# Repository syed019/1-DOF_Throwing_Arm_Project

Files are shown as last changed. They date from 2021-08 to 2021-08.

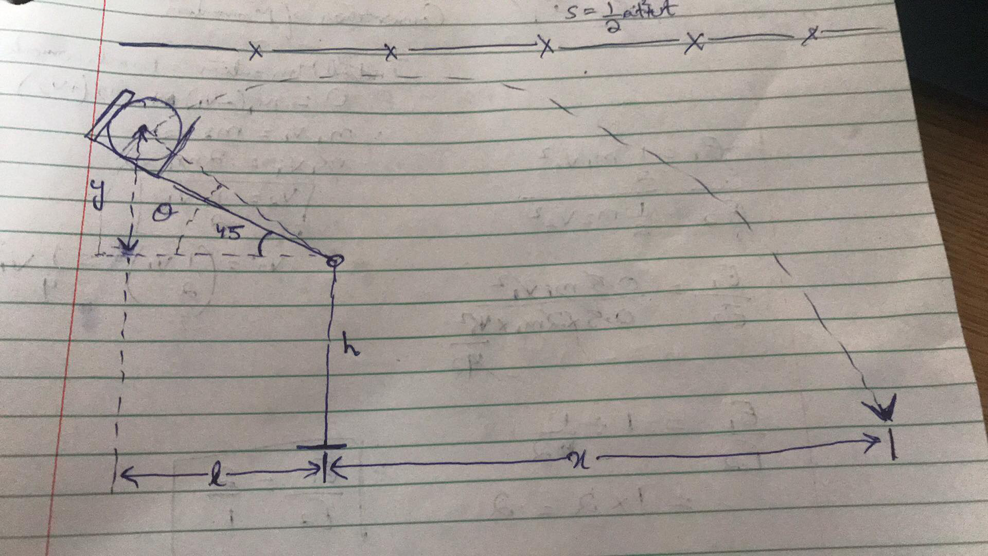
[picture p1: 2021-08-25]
Integration/1.jpg

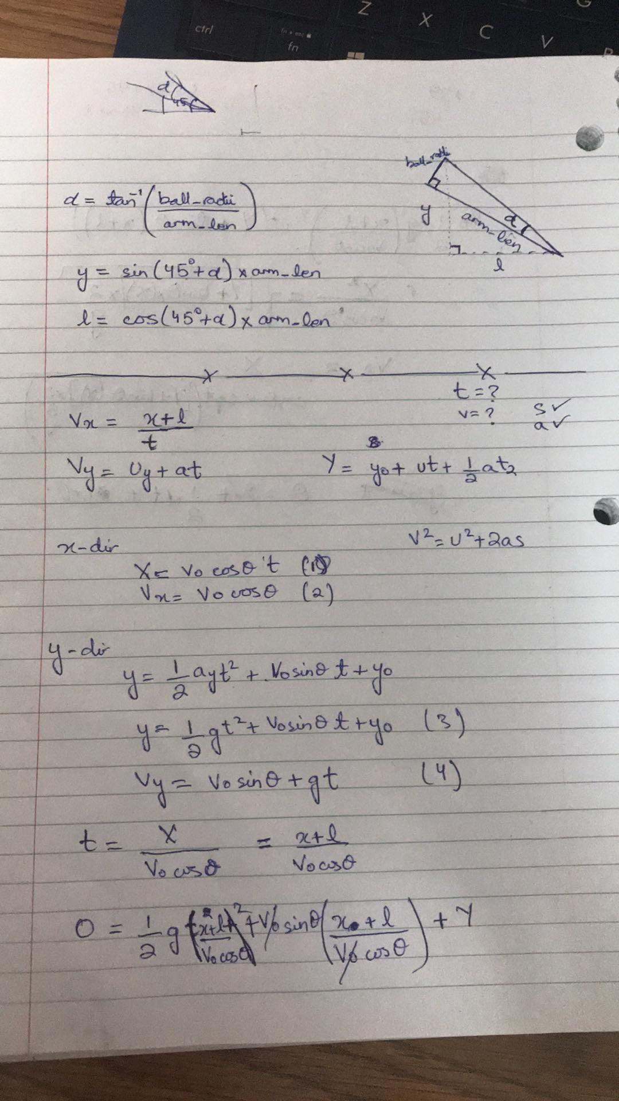
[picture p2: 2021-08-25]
Integration/2.jpg

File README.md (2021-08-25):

# MSE-312_Throwing-Arm-Project

   

This repository is for a course project (Mechatronics Design-II), taken at SIMON FRASER UNIVERSITY.

      The project consists of;
          1. Mechanical Design for a Throwing Arm (It's SOLIDWORKS design and MATLAB SIMSCAPE model)
          2. Electrical/Electronics DC-Moter Model, and it's Control Algorithm
          3. Overall Intergration of the Project

      Following are the team members for this project;
            1. Abdullah Tariq
            2. Junaid Jawed Khan
            3. Syed Imad Azeem Rizvi

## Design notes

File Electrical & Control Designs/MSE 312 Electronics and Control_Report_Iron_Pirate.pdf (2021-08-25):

# MSE312

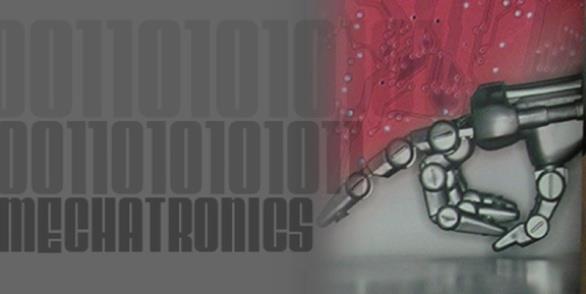
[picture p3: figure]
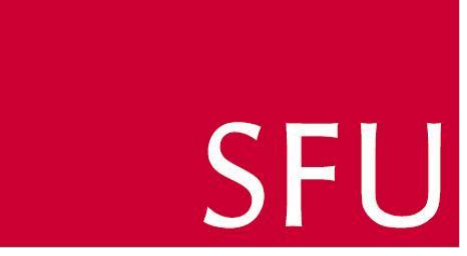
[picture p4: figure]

### ELECTRONIC & CONTROL DESIGN REPORT

Student Name | Student ID
Abdullah Tariq | 301297687
Junaid Jawed Khan | 301308300
Syed Imad Azeem Rizvi | 301297227

## Report due date: 25

th

## , JULY 2021

## Prepared for: Dr. Mehrdad Moallem

MSE-312 / MECHATRONIC DESIGN - II

MECHATRONIC SYSTEMS ENGINEERING

SCHOOL OF APPLIED SCIENCE

SIMON FRASER UNIVERSITY

i

## Table of Contents

ii

iii

## List of Figures

iv

Figure 31: Closed-Loop Speed Response | 34
Figure 32: Closed-Loop Position Response | 35

## List of Tables

Table 1: H-Bridge Cases Evaluation | 3
Table 2: Motor Comparison for RPM and Continuous Torque | 8
Table 3: Important results of each shortlisted motor | 10
Table 4: Simulink DC motor model parameters | 12
Table 5: GM8724S009 important parameters | 17
Table 6: Current, Speed and Position controller desired characteristics | 19
Table 7: Current Loop controller gains | 33
Table 8: Speed Loop controller gains | 34
Table 9: Position Loop controller gains | 35
Table 10: Open Loop Analysis | 36
Table 11: Closed Loop Analysis | 37

## 1. Introduction

The primary goal of this project was to develop a system for throwing a ball a predetermined

distance. We presented three different mechanical designs in the previous report, and after

analyzing their structures, we decided that the throwing ball bot would be our main design.

We will discuss three major aspects of the project in this report: electronic design, control design,

and their integration with our chosen mechanical design. As we are building a power circuitry for

driving a DC motor carrying an inertial load, the first section of the report will provide a detailed

analysis of its electronics. MOSFETs, H-bridges, and other necessary components are included in

the design, as well as an evaluation of their performance under various thermal conditions.

As we will be using a feedback controller to control the motor speed and position, the second part

of the project will involve implementing the control algorithm on our system. In this section, we

will first analyze our electronic system by determining its stability as well as the position of its

poles and zeros. Then, in accordance with that, we will construct a feedback loop comprised of

either P, PI, or a PID controller. Once the model for speed and position of motor control is created,

we will simulate our system and note different parameter values with different plots to obtain an

adequate value for the selected controller gains.

## 2. Electronic Design

This section of the report discusses the project's electronic design. To achieve the required

projectile motion for the ball, a DC motor is required to drive the throwing arm at a desired angular

velocity. The primary goal of this section is to design and simulate a power electronic drive

circuitry for a DC motor, which drives the arm used to throw the ball. We have included the

following components for the operation of the DC motor: An H-Bridge Circuit, a current sensor,

a PWM controlled voltage source, and a DC voltage source.

### 2.1. Power Circuitry Design

2.1.1. H-Bridge Circuit (TB6568KQ)

An H-bridge circuit is used to change the direction of a motor; in other words, it is an electronic

circuit that changes the polarity of a voltage-applied across the motor.

Figure 1 depicts a transistor-based H-bridge circuit. As seen in the diagram, two types of transistors

are used: PNP and NPN. We know from transistor electronics that when current is applied at its

base, the transistor will conduct. We can also note that the PN junction diodes are used as

freewheeling diodes, releasing electrical energy even when the motor is turned off.

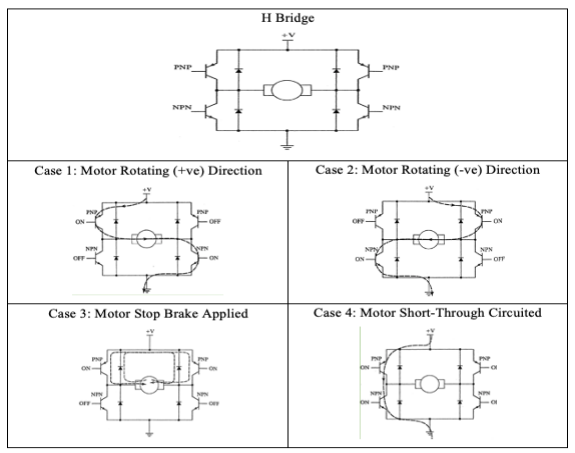
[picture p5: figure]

Figure 1: H-Bridge Operation Scenarios

Table 1: H-Bridge Cases Evaluation

SW1 | SW2 | SW3 | SW4 | MODE
OPEN | OPEN | OPEN | OPEN | OFF
CLOSED | OPEN | OPEN | CLOSED | CW
OPEN | CLOSED | CLOSED | OPEN | CCW
CLOSED | CLOSED | CLOSED | CLOSED | INVALID

With reference to Figure 1 and Table 1, if PNP (left) and NPN (right) are both turned on, the motor

will rotate clockwise. If both PNP (right) and NPN (left) are turned on, the motor will rotate

counterclockwise. If both left transistors are turned on and both right transistors are turned off, a

short circuit is formed. Dynamic or regenerative braking can be performed by turning on both

upper transistors while turning off both lower transistors. The duty cycle can be changed to control

the motor's speed.

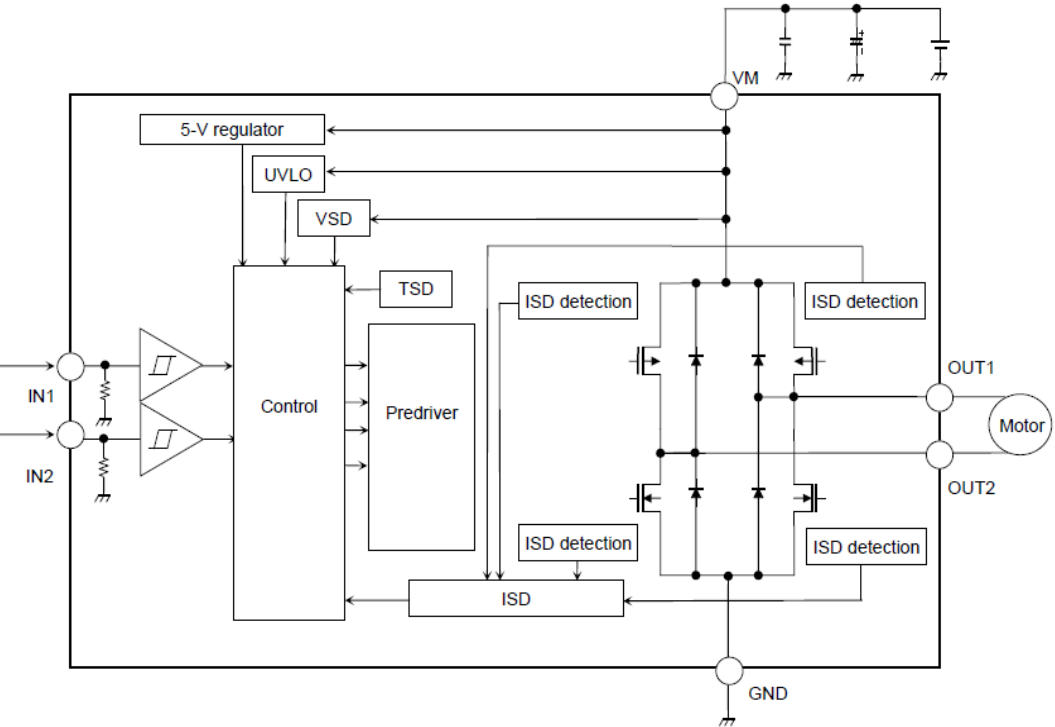
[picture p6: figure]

Figure 2: H-Bridge TB6568KQ

The motor driver we used for our motor control is the TB6568KQ. The functional block diagram

of the driver is shown in Figure 2. The TB6568KQ is a full bridge DC motor driver IC that uses

the MOS process for output power transistors. Aside from providing bidirectional motor control,

the IC includes several protection circuits that protect the motor from overcurrent, overvoltage,

thermal effects, undervoltage, and shoot through current.

Figure 3 is the data sheet of TB6568KQ H-bridge driver. This datasheet will be referenced in the

Heat Sink design section of this report.

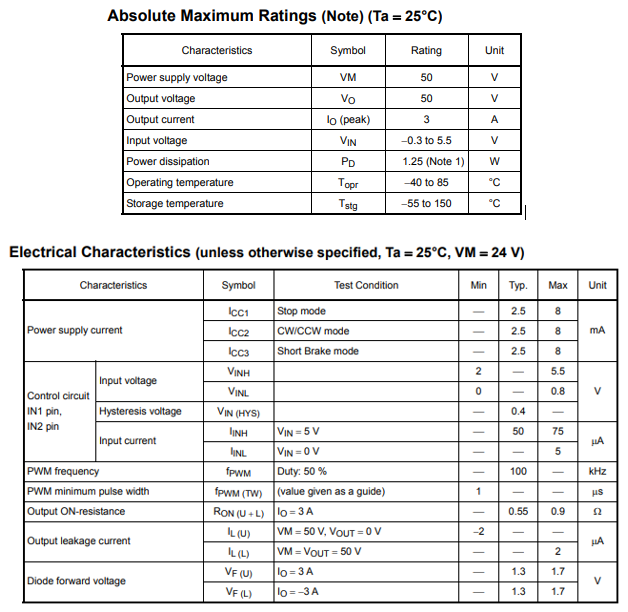
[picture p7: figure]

Figure 3: H-Bridge (TB6568KQ) Datasheet

2.1.2. Current Sensor

In our design, we will use a current sensor, which is an electronic device that detects current and

then generates a signal proportional to that value.

The basic principle for current sensing devices is that current flowing through a conducting wire

generates a magnetic field around it and uses two approaches: direct and indirect.

Direct sensing is based on Ohm's law, whereas indirect sensing is based on Faraday's and Ampere's

laws. As shown in Figure 4, we will use a built-in MATLAB Simulink block for current sensing

in our simulation.

Figure 4: Current Sensor Block

The use of a current sensor will be critical in the control portion of our project because we will

need to measure the armature current to implement feedback control of the motor current.

2.1.3. Heat Sink Design

Heat sinks are one of the most effective components for thermal management in electronics. Its

primary function is to direct heat away from the hot device. While operating, electronic

components can generate a significant amount of heat, and overheating can lead to component

failure. As a result, designing a heat manager for them is critical. The magnitude of heat generation

is directly related to power dissipation or the surface area of the electronic case from which power

is dissipated, the greater the power dissipation or the smaller the surface area, the greater the

generated heat. In other words, by increasing the surface area of our electronic case, we can reduce

the risk of overheating.

In our project, the major source of heat generation is the H-bridge driver (TB6568KQ). Figure 5

shows the thermal characteristics of this driver.

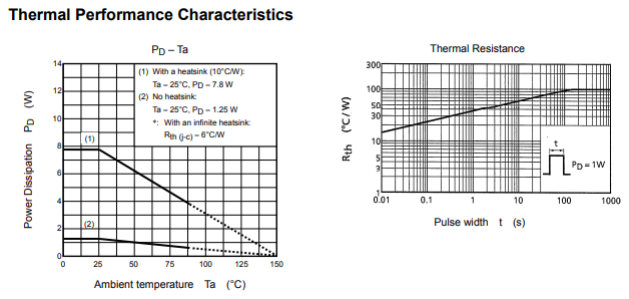
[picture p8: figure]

Figure 5: Thermal characteristics of H-Bridge.

The key point from the above figure is that if we operate our motor in the region covered by graph

2, we don't need a heatsink. However, if we want to run the motor anywhere between graphs 1 and

2, we'll need a heatsink to keep the H-bridge from overheating.

The thermal calculation for this component is as follows:

Based on the data sheet of TB6568KQ shown in Figure 5, the ambient temperature and maximum

junction temperature are defined as 25˚C and 150˚C.

The maximum power dissipated by the H-bridge can be calculated as in Equation 1.

PD = I0

2
∗ RH−bridge

PD = (3) ∗ (0.9)

PD = 8.1 Watts

Equation 1

Thermal resistance between the junction is defined as shown in Equation 2.

θjc = 6°c/w | Equation 2

The thermal resistance between junction and ambient can be calculated as shown in Equation 3.

θjc =

Tjunction,max − Tamb
PD

θjc =

150° − 25°
8.1

Equation 3

θjc = 15.43 c/w

The thermal resistance between the case and the ambient can be calculated as shown in Equation

4.

θJA = θCA + θJC

θJA = θCA − θJC

θJA = 9.432°c/w

θJA = 6°c/w

Equation 4

Finally, the case area required to dissipate the generated heat can be calculated as shown in

Equation 5.

Areq = (
50

θJA

)

2
cm²
Areq = 28.101 cm² | Equation 5

### 2.2. Motor Selection

We were given the option of choosing our own motor for this project. To complete the project's

deliverables, we selected the three motors listed below based on their respective features and

specifications that met our project requirements.

- Motor 1: GM8224S009
- Motor 2: C23-L33 W10
- Motor 3: PC280LG-011

Our goal is to simulate the operations of the three motors to evaluate their performance when

subjected to a desired inertial load.

Table 2 shows the important features of the three shortlisted motors. This table was populated

using the datasheets of the respective motor.

Table 2: Motor Comparison for RPM and Continuous Torque

Motor | Rated RPM | Rated Continuous Torque (Nm)
GM8224S009 | 720 | 0.1
C23-L33 W10 | 4700 | 0.117
PC280LG-011 | 8200 | 0.0255

Appendix A contains datasheets for the three motors that were shortlisted. In the following section,

we will analyze the behavior of the short-listed motors to choose our final motor for the controller

design.

2.2.1. Motors’s comparison:

In this section, the motors shortlisted in Section 2.2 are compared with each other. The Simulink

model in Figure 9 will be simulated with a duty cycle of 75% and the DC motor parameters will

be changed according to the shortlisted motors

Figures 6, 7 and 8 are the resultant currents, speed, and torque of each motor for a duty cycle of

75%.

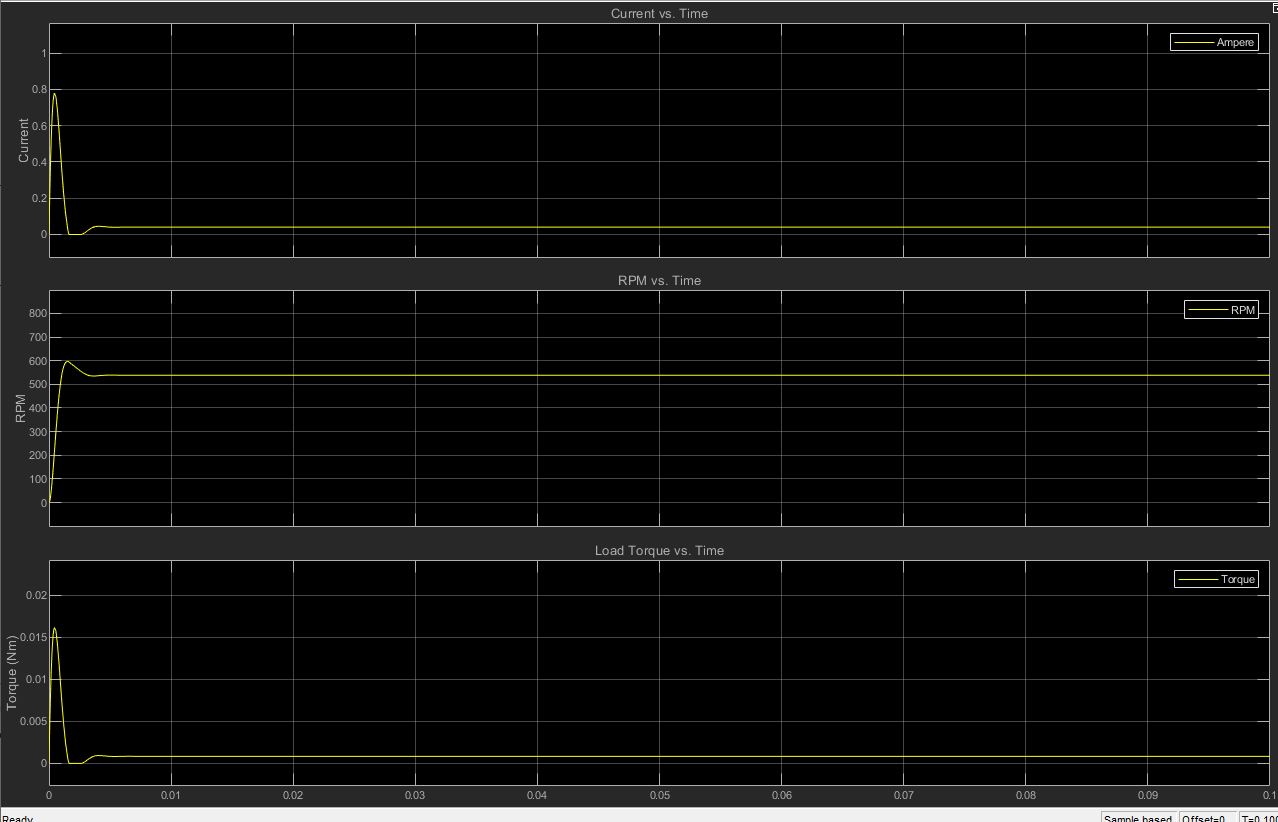
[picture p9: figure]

Figure 6: Motor 1 Resultant Current, RPM, and Torque for a 75% duty cycle.

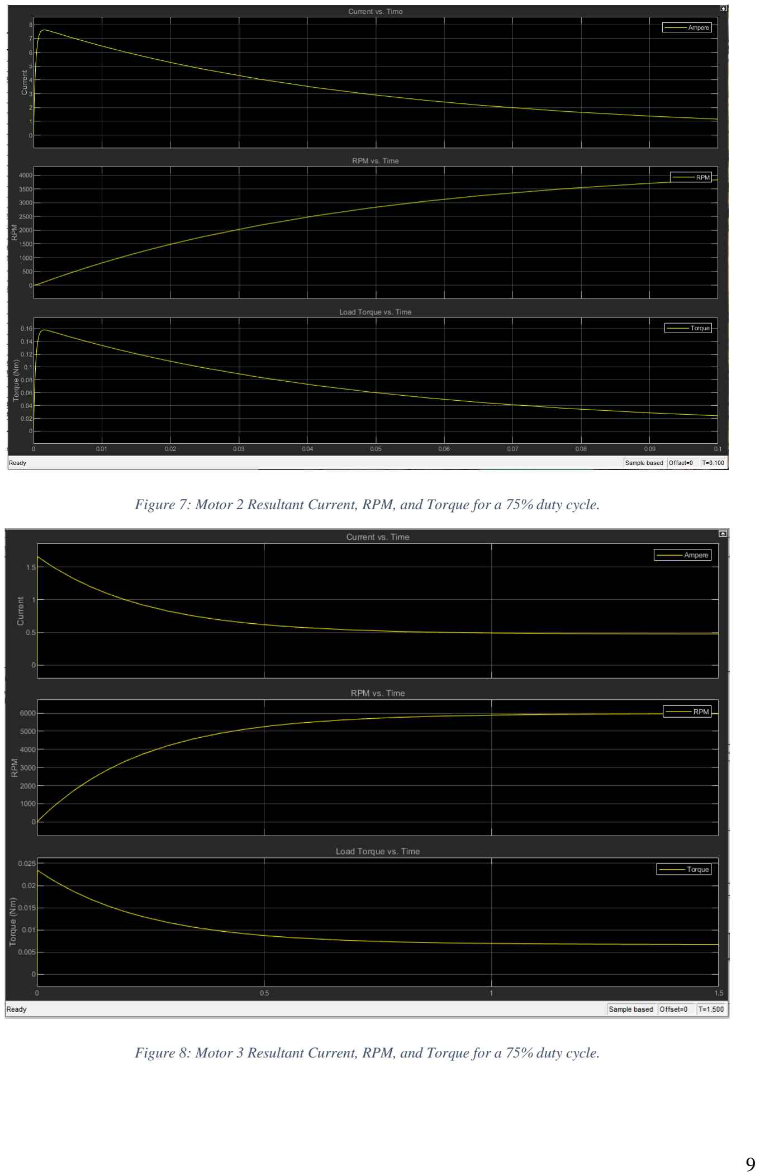
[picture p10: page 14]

Figure 7: Motor 2 Resultant Current, RPM, and Torque for a 75% duty cycle.

Figure 8: Motor 3 Resultant Current, RPM, and Torque for a 75% duty cycle.

Table 3 below illustrates the all the important parameters of each motor’s simulation results that

will be used for selecting the optimal motor for our project.

Table 3: Important results of each shortlisted motor.

Duty Cycle 75% | Motor 1 | Motor 2 | Motor 3
RPM | 539 rpm | 4370 rpm | 5970 rpm
Current | 40.62 mA | 233.575 mA | 474.797 mA
Torque | 8.41e-4 Nm | 4.461 e-3 Nm | 6.695e-3 Nm
Time to reach Steady State | 0.472 s | 0.353 s | 1.558s

The motor speed and torque data in the Table 3 were expected based on the motor data sheets in

Appendix A. Motor 3 has the highest no-load speed, whereas Motor 1 has the slowest. The system's

torque was greatest for Motor 3 to achieve its no-load speed. As higher torque is required to achieve

high speed, Motor 1 had the lowest torque due to its lower no-load speed.

Another important consideration when choosing a motor is the time it takes for the motor to reach

a steady state. According to Table 3, Motor 2 took the shortest time to reach steady state, while

Motor 3 took the longest.

Based on the preceding discussion, Motor 1 requires the least amount of electromagnetic torque to

generate enough rpm to drive the arm. As a result, we decided to use Motor 1 for our throwing

arm project. However, there is a trade-off between Motors 1 and 2 in terms of the time required to

reach no-load speed, but the time difference is not significant enough to affect our controller design

criteria.

### 2.3. Simulation of a DC Motor

In this section, we will first look at the simulation results of a DC motor using MATLAB Simulink

in three different scenarios:

1) PWM and Average Mode Simulation
2) With and Without Gear Reduction Simulation
3) With and Without Gear Reduction Simulation

The output behavior of motor parameters will be discussed and compared in each case, followed

by a comparison of the three shortlisted motors by varying the duty cycle of their PWM signal.

Figure 9 shows the designed Simulink model of a DC motor employed for analysis in this section

of the report.

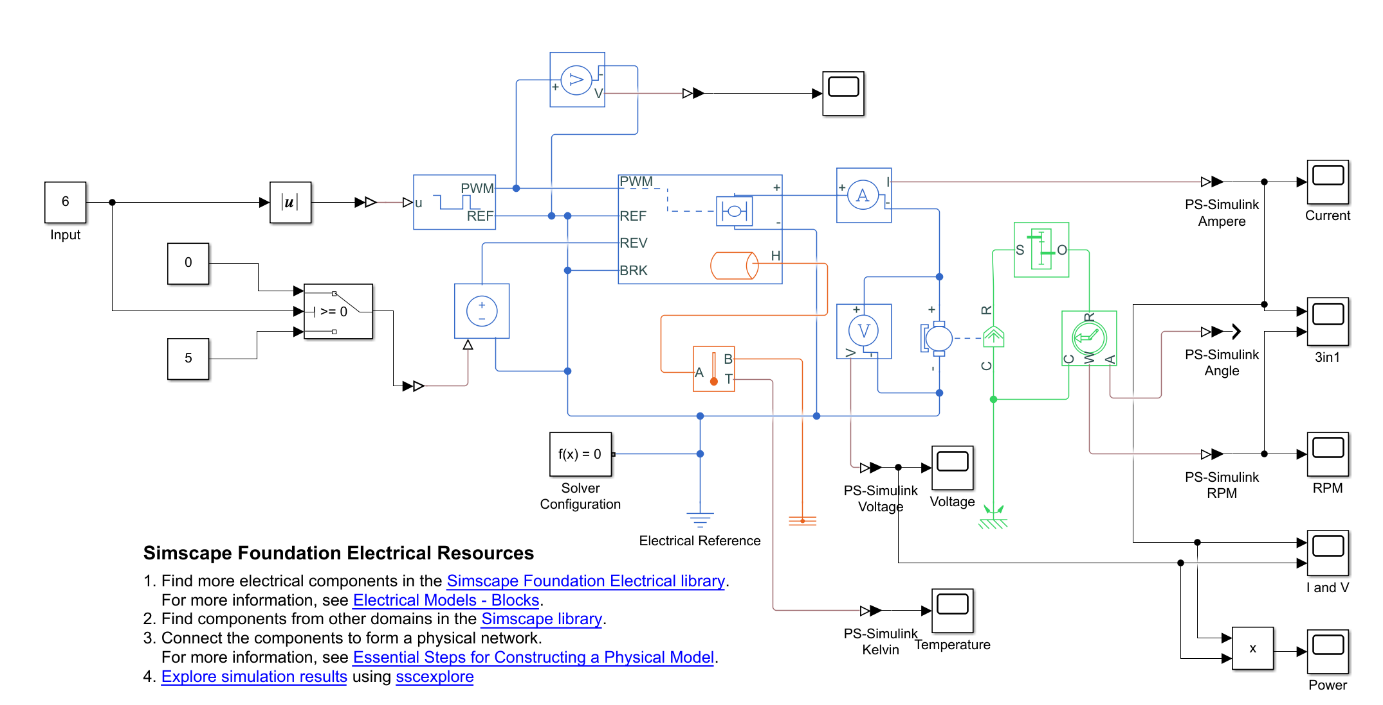
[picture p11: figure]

Figure 9: Simulink Model of a DC Motor

The parameters of the PWM, H-bridge and motor block used in the above Simulink model are

shown in Table 4.

Table 4: Simulink DC motor model parameters.

Parameters | Values

Controlled PWM Voltage

PWM Frequency | 4000Hz
Input value 0% DC | 0
Input value 100%DC | 12
Output Voltage | 12

H-Bridge

Total bridge on resistance | 0.55 ohms
Freewheeling diode on resistance | 1.3/3 ohms
Measurement temperature | 298.15 K
Freewheeling diode off-state conductance | 1e-6 S
Total bridge on resistance at second measurement temperature: | 0.9 ohms
Freewheeling diode on resistance at second measurement temperature | 1.7/3
Second measurement temperature | 303.15 K

DC Motor

Armature inductance: | 2.34 mH
Stall torque: | 3.01e-1 N*m
No-load speed: | 720 rpm
Rated DC supply voltage: | 12 V
Rotor inertia: | 2000 g*cm^2
Rotor damping: | 1e-04 N*m/(rad/s)

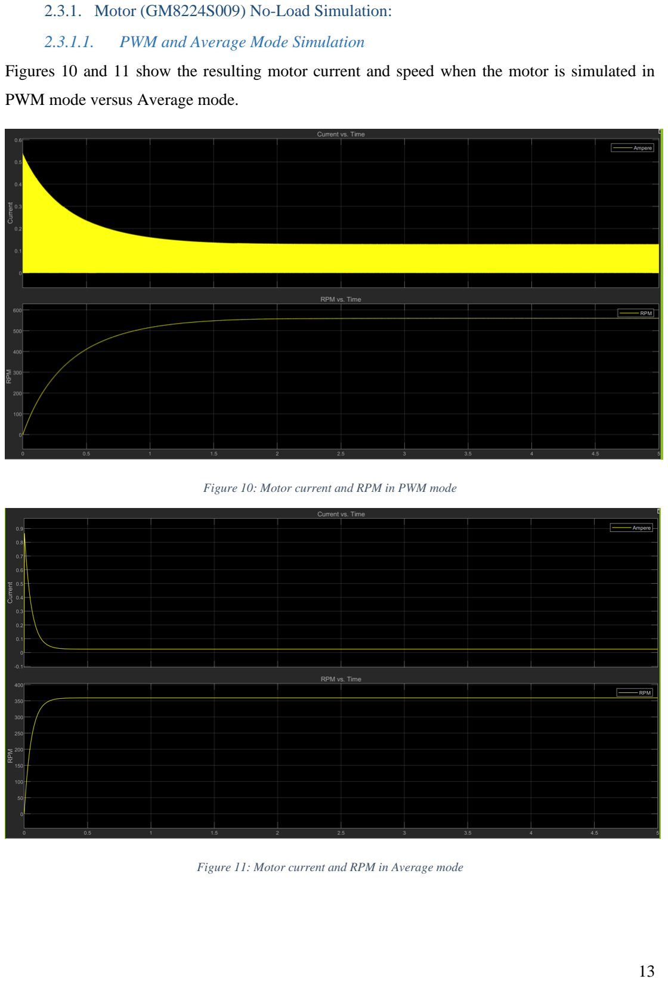
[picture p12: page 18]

2.3.1. Motor (GM8224S009) No-Load Simulation:
2.3.1.1. PWM and Average Mode Simulation

Figures 10 and 11 show the resulting motor current and speed when the motor is simulated in

PWM mode versus Average mode.

Figure 10: Motor current and RPM in PWM mode

Figure 11: Motor current and RPM in Average mode

In this case, two simulation modes, PWM and average mode, are compared. The simulation duty

cycle is set to 50%. First, we ran our model in PWM mode, and Figure 10 shows the results. The

plot shows that in PWM simulation mode, current output switches between high and low, while

the duration for a pulse to be high or low is the same due to the applied 50% duty cycle. In average

mode, the current output does not switch between high and low because the average of the PWM

pulse is applied to the motor.

When we compare the RPM plots in both cases, we can see that the average mode RPM rise time

is shorter than the PWM mode. In average mode, RPM reaches steady state in less than 0.25

seconds, whereas it takes 2 seconds in PWM mode.

2.3.1.2. With and Without Heatsink Simulation

Figures 12 and 13 show the resulting temperature when the motor is simulated without a heatsink

versus with heatsink for the H-bridge.

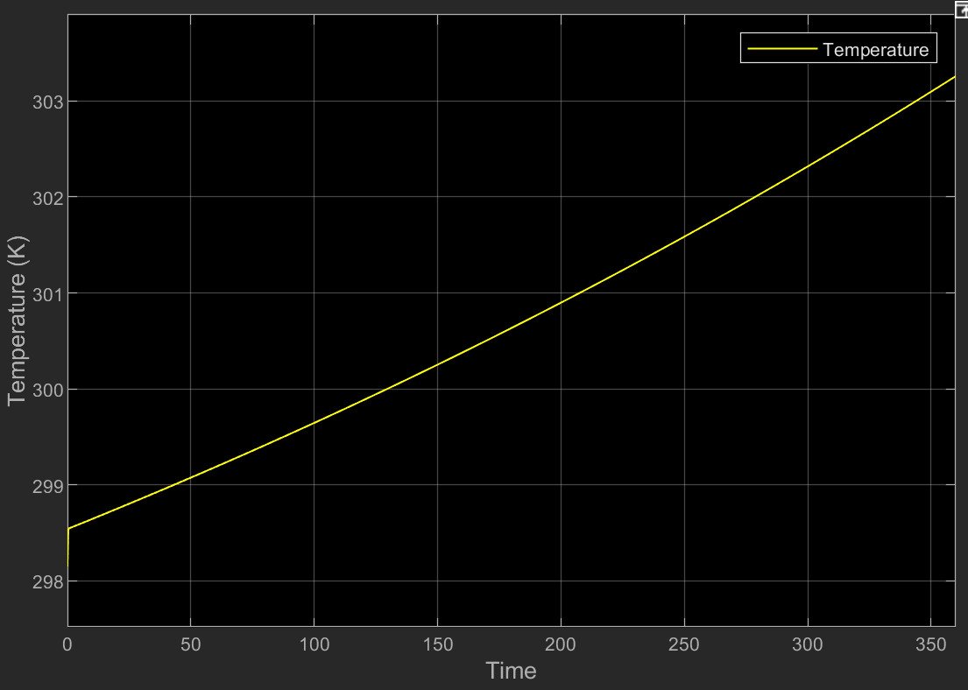
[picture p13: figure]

Figure 12: H-bridge temperature without heatsink

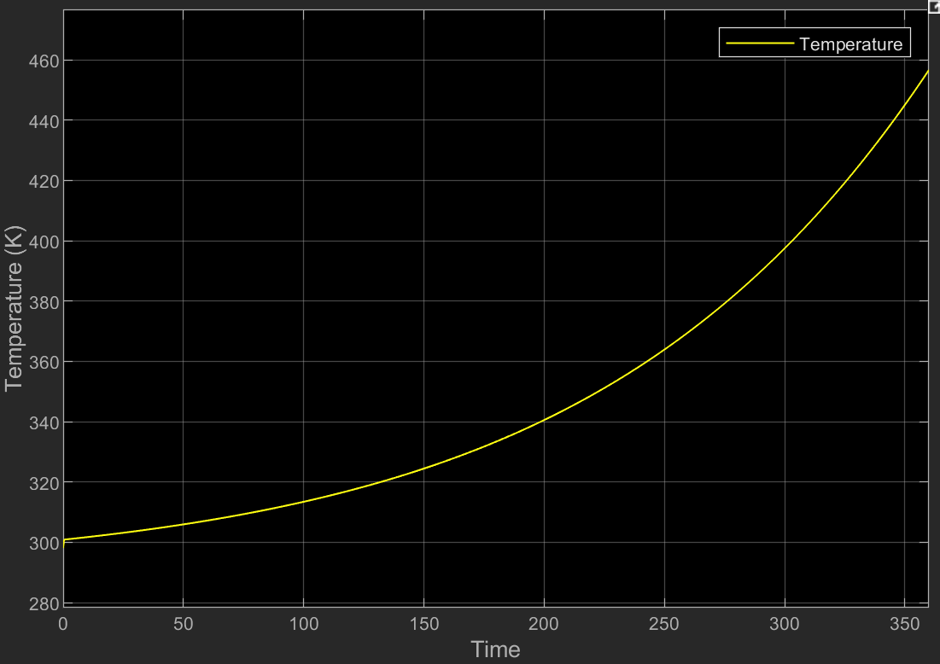
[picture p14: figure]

Figure 13: H-bridge temperature with heatsink

While running, electronic components generate heat; it is critical to consider the effect of heat

sinks on the system, as excessive heat generation can cause component failure.

Figure 12 depicts the temperature rise over time when no heat sink is used; it is important to note

that after 200 seconds, the temperature rises at an increasing rate. Now, if we look at Figure 13,

we can see how efficiently the heat sink affects the system, as the temperature with the heat sink

is around 303K at time 350 seconds, but it is at 450K without the heat sink. The purpose of a heat

sink is to increase the surface area of the cover so that heat generated during operation has more

surface area to escape from the system.

2.3.1.3. With and Without Gear Reduction Simulation

Figures 14 and 15 show the resulting rpm when the motor is simulated with a gear box versus

without a gearbox at the output.

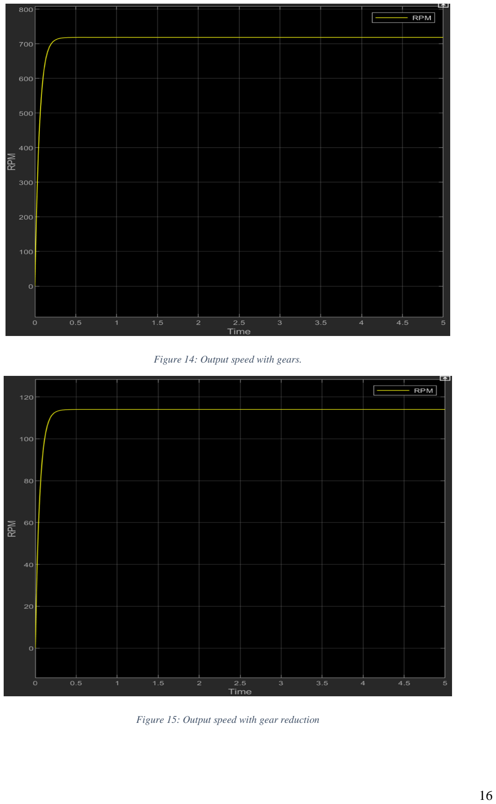
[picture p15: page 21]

Figure 14: Output speed with gears.

Figure 15: Output speed with gear reduction

Concept of gear reduction is quite straight forward; Gear reduction is as shown in Equation 6.

New RPM =

No load speed
gear ratio

New RPM =

720
6.3

= 114.2

Equation 6

Figure 14 depicts a situation in which there is no gear reduction; the plot shows that RPM is equal

to the motor's no-load speed, as shown in Table 3. In Figure 15, gear reduction is used because the

gear ratio is 6.3. The final RPM obtained is 114, which is equal to the calculated equation 6.

## 3. Controller Design

In most control systems, a simple unity feedback is not sufficient for achieving the desired output.

Therefore, a controller is typically added to the system to minimize the error measured and desired

output. There are several ways to design a feedback controller for your plant. However, the most

common design approach for a motor-controlled application is the cascaded design approach.

The cascaded design approach allows for the motor control to be decoupled into three feedback

loops, with the innermost loop being the fastest and the outermost loop being the slowest. The

cascaded design approach enables the fastest inner loop to deal with disturbances while ensuring

that the controlled variable does not deviate significantly from the desired set point.

As mentioned in the previous section, we were given the option in this project of choosing our

own DC motor for our project. We chose Motor 1 because it has a decent rated speed, continuous

torque, and is affordable based on our budget.

The selected DC motor is GM8724S009, and its parameters are shown in Table 5

Table 5: GM8724S009 important parameters

Motor Parameter | Symbol | Value
Rated DC Voltage | V | 12
Armature Resistance | R | 4.33
Armature Inductance | L | 2.34e −3
Damping Constant | B | −4 1.1e

Torque/Back-emf Constant | Km | −2 2.18e
Rotor Inertia | J | 2.3e −4
Gear Ratio | n | 6.3
Gear efficiency | η | 0.95
Total Inertia | Jtotal | −3 8.3e

### 3.1. Design Criteria

There are no fixed requirements for settling-time, overshoot, or steady-state error in this project

because we are free to choose our own motor and tune it to meet our needs.

To launch a ball to the specified target, the rotating arm will go through three stages. The arm will

accelerate to the desired angular velocity in the first stage, then continue at the desired angular

velocity until it reaches the desired launch time in the second stage. At the time of launch, the

rotating arm is in stage 3 and will return to its initial position after the ball has been launched. In

summary, the first two stages control the motor's speed, while the final stage controls the motor's

position.

Table 6, and Figures 16 and 17, lists the design specifications for the rotating arm’s current, and

speed.

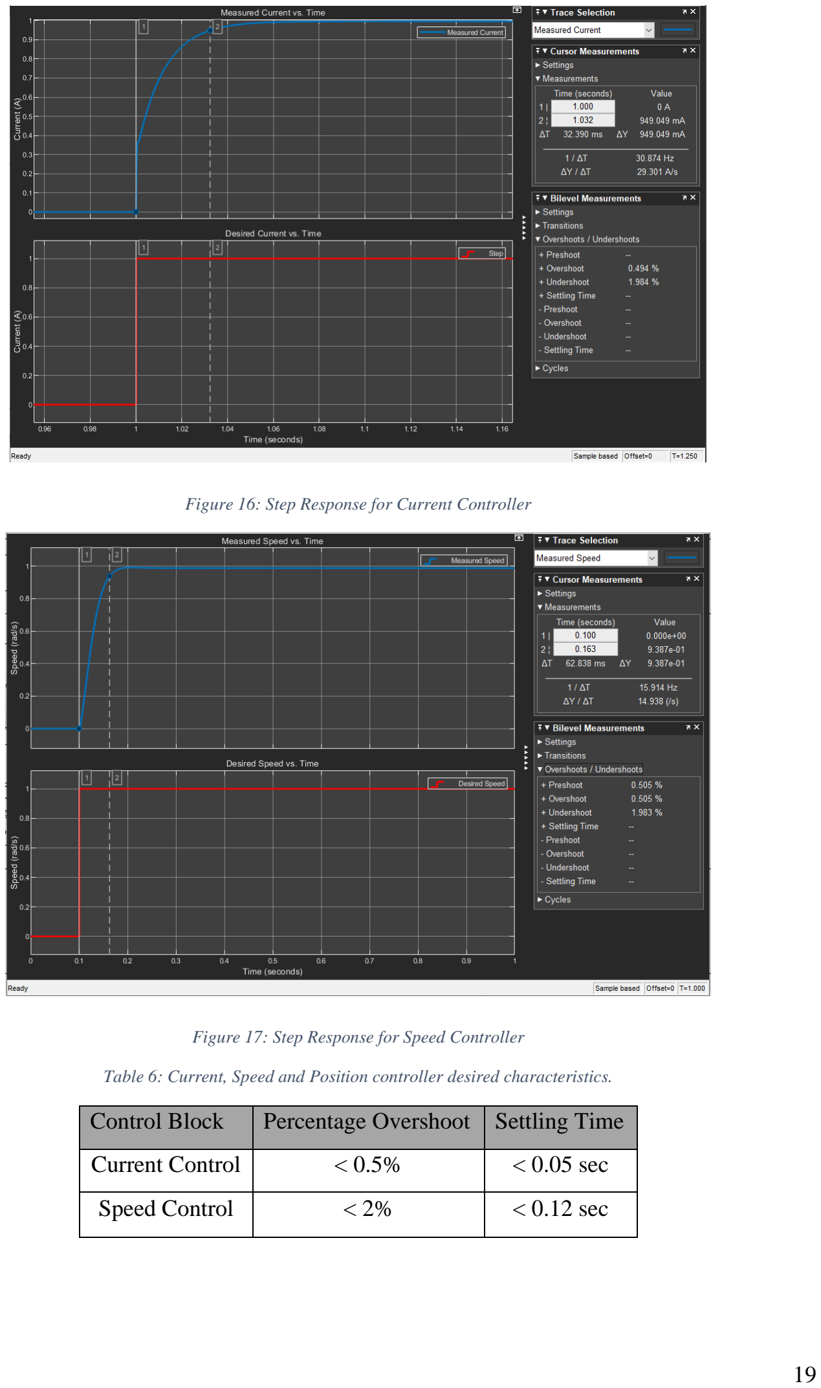
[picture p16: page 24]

Figure 16: Step Response for Current Controller

Figure 17: Step Response for Speed Controller

Table 6: Current, Speed and Position controller desired characteristics.

Control Block | Percentage Overshoot | Settling Time
Current Control | < 0.5% | < 0.05 sec
Speed Control | < 2% | < 0.12 sec

Based on the step-response behavior of the current and speed controller blocks, the tabulated value

in table 6 establishes the boundary conditions for our controller design criteria.

We want the current and speed controllersto be as robust as possible; because the current controller

is the fastest, we want it to settle quickly with minimal overshoot so it can handle disturbances.

Once the current controller is tuned properly, the speed, and position controllers can handle a little

delay.

### 3.2. System Modelling

3.2.1. Motor Equation

The motor receives voltage as input, and it produces torque as an output. This is illustrated

graphically, as shown in figure 18.

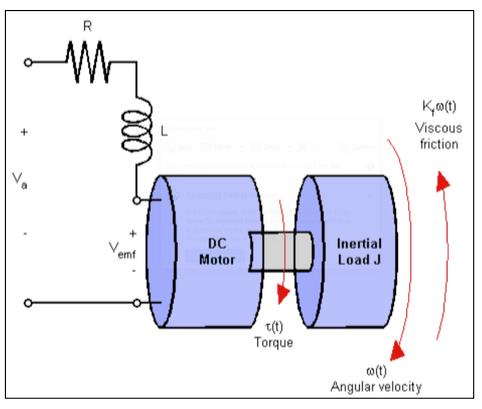
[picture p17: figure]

Figure 18: Graphical model of motor and connected load.

Based on Figure 18, the input voltage rotates the shaft of the motor, which is connected to an

inertial load, the rotation of the motor shaft rotates the inertial load. Some assumptions that are

made in this model are that the rotor and shaft of the motor are rigid, and friction is proportional

to the speed of the motor.

The electrical energy from the motor’s circuitry is converted to mechanical energy using a torque

transducer.

The electromechanical equation relating the electrical system and the mechanical system is shown

in equation 7

V = L

di
dt + Ri + e

Equation 7

Where the generated back-emf is relative to the angular velocity, gear ratio( n) and motor constant

(Km) as shown in Equation 8.

e = Kmnθ̇ | Equation 8

The net torque that is applied to the connected inertial load is as shown in Equation 9

τ − τfriction = Jθ̈ | Equation 9

Where, the motor torque is related to the armature current by the motor constant (Km), gear

efficiency and gear ration, as shown in equation 10.

τ = ηKmni | Equation 10

The friction torque comprises of load resistance and frictional torque of the motor, resulting in the

net torque produced by the motor as shown in equation 11.

τ − Bθ̇ − τload = Jθ̈ | Equation 11
3.2.2. Transfer Functions

Appling Laplace transformation on equations 7 and 11, we get the results shown as equations 12

and 13.

V(s) = LsI(s) + RI(s) + Kmnsθ | Equation 12

ηKmnI(s) − Bsθ(s) − τload = Js

2θ(s) | Equation 13

Assuming zero initial conditions, we can control the position and angular velocity of the inertial

load by controlling armature current of the motor.

Using equations 12 and 13, it can be shown that the transfer function relating angular velocity of

the inertial load and the voltage applied at the motor terminals is as shown in equation 14.

θ̇(s)
V(s)

=

ηKmn
(Ls + R)(Js + B) + ηKm

2 n

2

Equation 14

Taking the integral of the angular velocity shown in equation 14, the transfer function relating

angular position and voltage applied across the motor are related as shown in equation 15.

θ(s)
V(s)

=

ηKmn
s[(Ls + R)(Js + B) + ηKm

2 n

2]

Equation 15

The motor parameters in Table 5 are plugged into equation 15. The result is shown in Equation 16.

θ(s)
V(s)

=

3324.1
s(s + 1850)(s + 0.843)

Equation 16

Figure 19 shows the root locus of the transfer function shown in Equation 16.

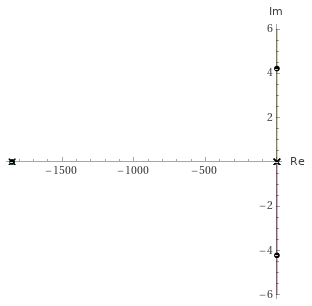
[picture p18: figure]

Figure 19: Root-locus of motor transfer function.

Based on Figure 19, the pole at the far left is at 1850, which corresponds to the inverse of the

electrical time constant (R/L). Because this pole is relatively far away from the imaginary axis, it

has a negligible effect on overall system performance. The poles and zeros closest to the imaginary

axis have the most influence.

Based on these pole placements, we can conclude that the mechanical time constant is much larger

than the electrical time constant, and this conclusion leads to Cascade control, a popular method

of motor control in the industry.

### 3.3. Cascade Control Scheme

A cascade control strategy consists of inner and outer control loops, with the inner loop being the

fastest and the outer loop being the slowest. The fastest loop in motor control applications is the

current control, and the slowest is the angular position control.

In this section, we look at the transfer function of the inner current loop, followed by cascaded

outer speed loop with inner current loop, and finally the outer position loop cascaded with inner

speed and current loop.

3.3.1. Current Control

Figure 20 shows the block diagram of a typical DC motor corresponding to the transfer function

represented in Equation 15.

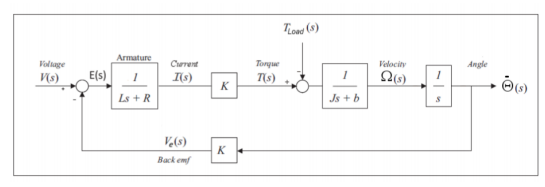
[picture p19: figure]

Figure 20: Block diagram of DC motor control.

Rearranging the block diagram for a transfer function of armature current as output we get the

transfer function shown in equation 17.

I(s)
V(s)

=

J(s +

B
J

)

[(Ls + R)(Js + B) + ηKm

2 n

2]

Equation 17

In Equation 17, we can note that the characteristic equation is the same shown in Equation 17 with

a zero at -

B
J

This new zero is close to the pole represented by the inverse of your mechanical time constant.

The poles are attracted to zeros by using a feedback loop with gain. As a result, the pole represented

by the inverse mechanical time constant can be cancelled with the new zero, allowing us to

approximate the second order transfer function shown in Equation 17 with a simple purely

electrical first order transfer function shown in Equation 18.

I(s)
V(s)

=

1
L
[s +

R
L

]

Equation 18

The approximation shown in equation 18 allows you to decouple the electrical and mechanical

part of your controller, i.e., the torque and the trajectory generation. The following is the control

loop for current control, where the motor transfer function is represented by equation 18.

Figure 21: Block diagram of current loop.

The controller block in figure 21 could be a simple P, PI, PD, or PID. Each combination has

different effects on the system.

3.3.1.1.1. Controller Choices

The P controller is simply an amplifier that provides a proportional constant based on the error. A

simple P controller will have a slow/sluggish response if the gain is small, and a too aggressive

response if the gain is high, resulting in an overshoot and large steady state error.

A PI controller will aid in reducing the steady-state error introduced by a simple P controller. A PI

controller, on the other hand, slows response time and decreases system stability. Furthermore,

with this controller, the output rise times cannot be reduced.

A PD controller improves system stability by analyzing error changes and adjusting gain to

minimize overshoot. A PD will reduce overshoot while increasing steady-state error.

A PID controller provides us with optimal control for fast response, minimal steady-state error,

and increased stability.

We chose a PI controller to design the current loop because the zero generated by the PI controller

is used to cancel the pole at R/L shown in Equation 18, allowing us to control the current by

changing the gains of the PI control block.

The closed-loop transfer function of the current loop with a PI controller to cancel motor pole at

R/L is as shown in equation 19.

I(s)measured

I(s)desired

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
Equation 19

Where, Kp
Ls

is the open loop gain of the system shown in figure 19.

Moreover, the value Kp
L

is the bandwidth of the closed loop system, which should be orders of

magnitude small in comparison to the sampling frequency of the closed loop system for a practical

implementation of this controller. More on the sampling frequency and tunning of this inner loop

is presented in the Integration section.

3.3.2. Speed Control

The angular speed of the motor is controlled by speed controller cascaded to the current control

loop presented in the previous section as shown in Figure 21.

Figure 22: Block diagram of cascaded speed loop.

The inner current loop shown in figure 22 will convert the desired torque into current equivalent

using the torque constant of the motor as shown in equation 20.

τdesired = KmnIdesired | Equation 20

For a practical implementation of a cascaded speed controller, the bandwidth of the closed loop

system shown in Figure 22 should be orders of magnitude lower than the bandwidth of the Current

Control loop shown in Figure 21.

The available controller choices of the speed controller are the same as presented in the previous

Current Control section. The details on the selected controller and tunning are presented in the

Integration section of this report.

3.3.3. Position Control

The angular position of the motor is controlled by a position controller cascaded to the speed

control loop presented in the previous section, as shown in Figure 23.

Figure 23: Block diagram of cascaded position control.

For a practical implementation of a cascaded position controller, the bandwidth of the closed loop

system shown in Figure 23 should be orders of magnitude lower than the bandwidth of the Speed

Control loop shown in Figure 22.

The available controller choices of the position controller are the same as presented in the previous

Current Control section. The details on the selected controller and tunning are presented in the

Integration section of this report.

3.3.4. Trajectory Tracking

Figure 23 in the preceding subsection depicts the final cascaded control of a DC motor. After

launching the ball, the DC motor is expected to return to its starting position in our project.

Trajectory Control is used to achieve this.

For each launch of a ball to a target location, a DC motor goes through three stages. The DC motor

ramps up to a cruise speed in stage one, maintains the cruise speed in stage two, and ejects the ball

at the predetermined target angle in stage three. In stage three, after launching the ball, the motor

should return to its original resting position in preparation for the next target location.

Trajectory tracking is used to return the motor to its initial state. The trajectory controller is only

activated at the end of the motion. The goal here is to define a speed profile that will be used to

toggle between speed and position control. Only the speed and current loops are active in stages

one and two, and only the position and current loops are active in stage three, i.e., torque commands

in stages one and two are based on speed error, and torque commands in stage three are based on

position error. Figure 24 depicts a typical speed profile of DC motor used for launching a target.

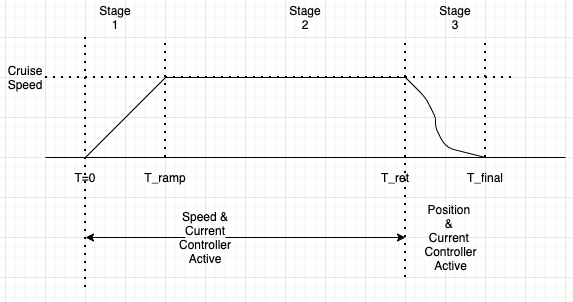
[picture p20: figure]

Figure 24: Three stages of a cascaded control of a DC motor.

According to Figure 24, after launching the ball at a predetermined retraction time, the motor

returns to its initial state at stage three. Because we have six constraints: the angular position,

velocity, and acceleration of the motor at the start of stage three and the desired angular position,

velocity, and acceleration to return the motor to its initial state, the profile shown in stage three is

approximated using a fifth-degree polynomial.

The six constraints can be satisfied using a quintic trajectory profile. This profile is formulated as

shown in Equation 21.

q(∆t) = q0 + q1∆t + q2∆t

2 + q3∆t

3 + q4∆t

4 + q5∆t

5 | Equation 21

Where 0 ≤ ∆t ≤ Tfinal − Tretraction

q0, q1, q2, q3, q4, q5 can be determined using the information we have from observing the speed

profile in stage three of Figure 24.

When ∆t = 0, q0, q1 and q2 can be determined as shown in Equation 22.

q = qretraction = q0,
q̇(∆t = 0) = q1 = ωcruise, q̈(∆t = 0) = 2q2 = q̈desired at Tretraction | Equation 22

When ∆t = Tfinal − Tretraction:

By using the results shown in Equation 22 and solving the three equations q(∆t) = 0, q̇(∆t) =

0, q̈(∆t) = 0 simultaneously, we can calculate q3, q4,& q5 and generate a trajectory profile that

has a speed profile as shown in Figure 24

To control the torque of the motor such that the angular position, velocity, and acceleration follow

the desired profile represented by q, q̇, and q̈, we use a PID controller. The motion planner

function is provided in the Appendix B for your reference.

## 4. Integration of Electronics and Control

In this section, we will simulate the theory discussed in sections 2 and 3 and analyze the results.

This section integrates the electrical and control of the motor with specified load values.

Before fine-tuning our control parameters, we developed a desired kinematic profile for our system

to follow. Figure 25 depicts the kinematic profile that will be used in our control system.

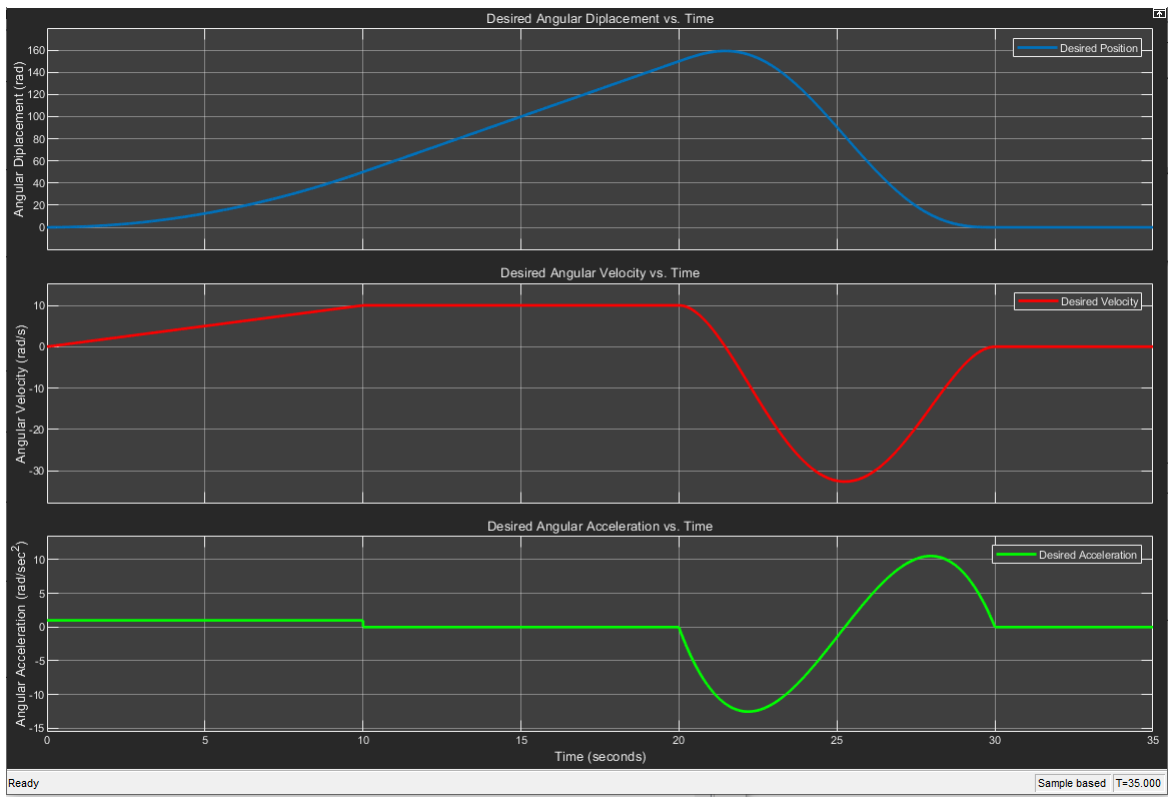
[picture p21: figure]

Figure 25: Kinematic Profile for the Project

Based on Figure 25, a quintic polynomial is employed to represent our desired velocity profile and

computed the corresponding displacement and acceleration profiles as described below:

- In the interval 0 – 10 sec, the speed is ramping up to 10 rad/s at a constant rate. Therefore,

the acceleration in this interval is constant while the angular position is increasing

parabolically.

- In the interval 10-20 sec, the speed maintained at 10 rad/s. Therefore, the acceleration in

the interval is zero while the angular displacement increases linearly.

- In the interval 20 – 30 sec, the ball is launched at an angular velocity of 10 rad/s and the

structure experiences a negative acceleration to return to the initial state for the next target.

- In the interval 30 – 35 sec, the structure has returned to its initial state as all quantities go

to zero.

### 4.1. Simulation Results

4.1.1. Open-Loop System Response

To simulate the system response, we provide our system with a predefined kinematic profile for

open-loop analysis. Each PID block has the gain values Kp = 1, Ki = 0, and Kd = 0, i.e., a simple

gain with no controller. The current, speed, and position controller blocks are cascaded together in

Simulink as shown in Figure 26.

Figure 26: Cascaded position, speed, and current controls.

Figure 26 shows an intuitive system block diagram for the open-loop response. The system is

without a feed-back and behaves erratically. Figures 27, 28, and 29 are the respective plots for the

current, speed, and position subsystems. These plots are analyzed in the Performance Evaluation

section.

4.1.1.1. Current Control

Figure 27 depicts the open-loop current response with the desired kinematic profile.

Figure 27: Open-loop current response.

4.1.1.2. Speed Control

Figure 28 depicts the open-loop speed response with the desired kinematic profile.

Figure 28: Open-loop speed response.

4.1.1.3. Position Control

Figure 29 depicts the open-loop position response with the desired kinematic profile.

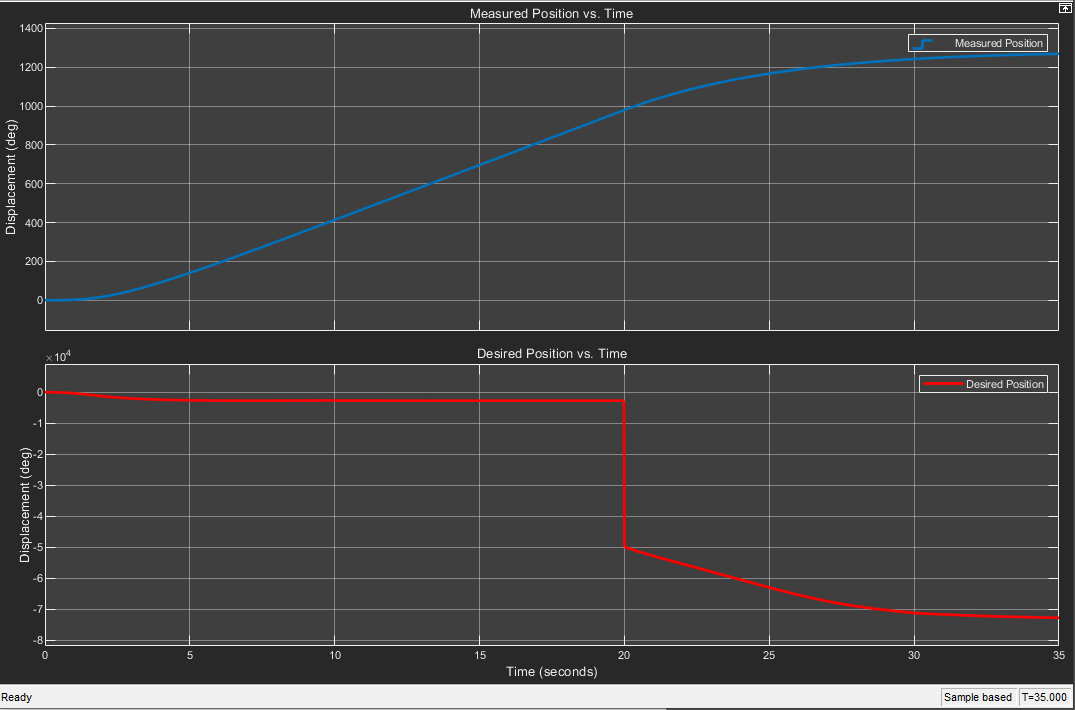
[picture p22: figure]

Figure 29: Open-loop position response.

4.1.2. Closed-Loop System Response

For the closed-loop analysis of each controller subsystem, the three respective controllers are in a

nested loop as presented in Figures 21, 22, and 23, where the current controller (fast) block is

inside the speed controller (moderate) block, and speed controller block is inside the position

controller block (slow).

4.1.2.1. Current Control

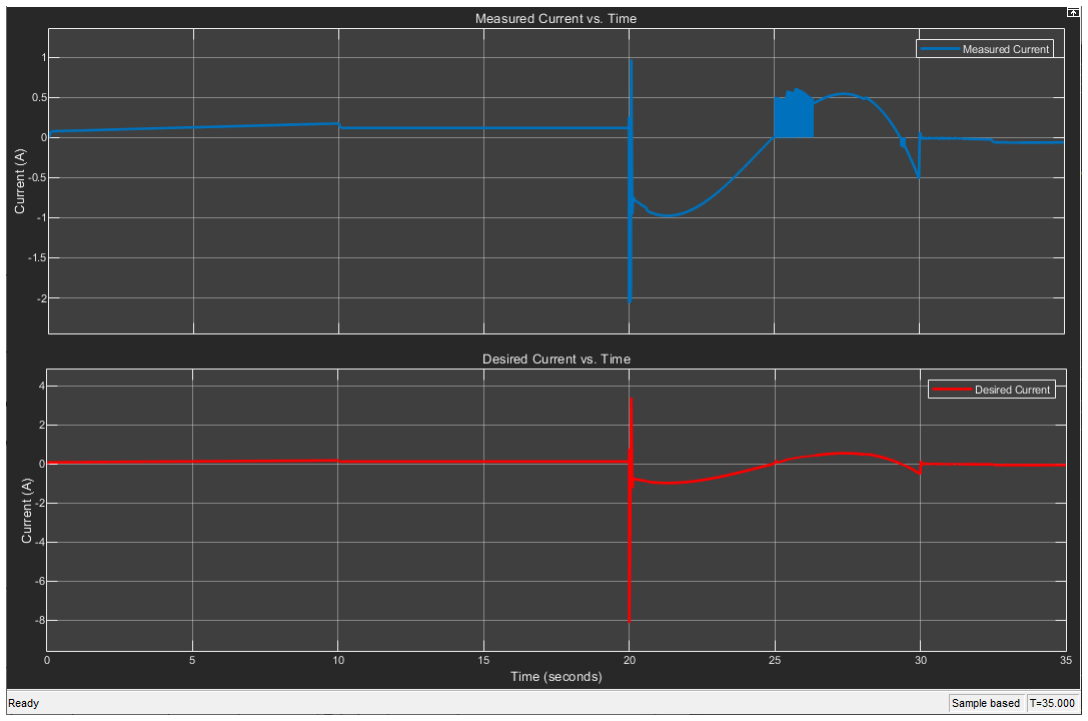
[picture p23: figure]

Figure 30: Closed-Loop Current Response

Figure 30 depicts the desired kinematic profile of the closed-loop current response. We tune the

current controller parameters as shown in Table 7 based on the discussionsin Section 3 and Current

Control about the bandwidth frequency and dominance of the electrical time constant.

Table 7: Current Loop controller gains.

Gain | Value
Kp | 2 ∗ π ∗ fs ∗ L
Ki | 2 ∗ π ∗ fs ∗ R ∗ (1/20)
KD | 0

Where, (1/20) is the correction factor for the integral controller and fs is the sampling frequency
used in the simulation. We set our sample time to be 1
4000

and this gave us smooth current, velocity,

and position plots.

4.1.2.2. Speed Control

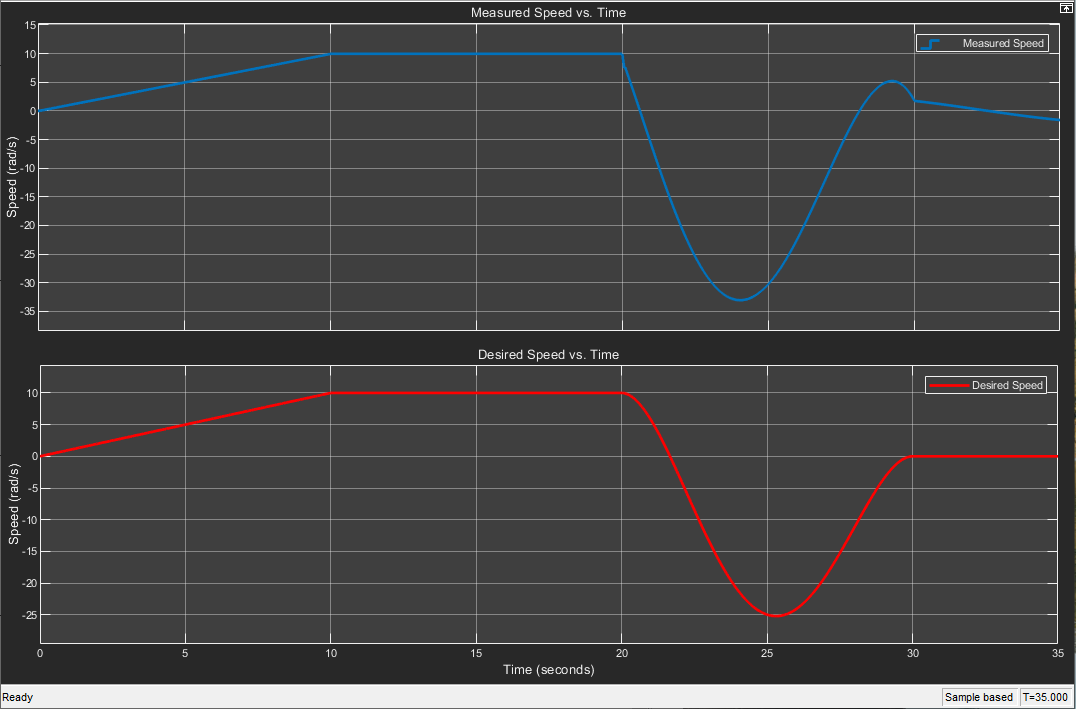
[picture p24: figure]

Figure 31: Closed-Loop Speed Response

Figure 31 shows the closed-loop speed response with desired kinematic profile. Based on the

discussions in Section 3 and Speed Control section, regarding the bandwidth frequency of this

speed loop being orders of magnitude lower than the inner current loop, we tune the current

controller parameters as shown in Table 8.

Table 8: Speed Loop controller gains.

Gain | Value
Kp | 2 ∗ π ∗ fs ∗ L ∗ (1/10)
Ki | 0.0132
KD | 0.001

Where, (1/10) is used to reduce the bandwidth of the speed controller by 10 times in comparison

to the inner current loop and fs
is the sampling frequency used in the simulation. We set our sample time to be 1
4000

and this gave us smooth current, velocity, and position plots.

4.1.2.3. Position Control

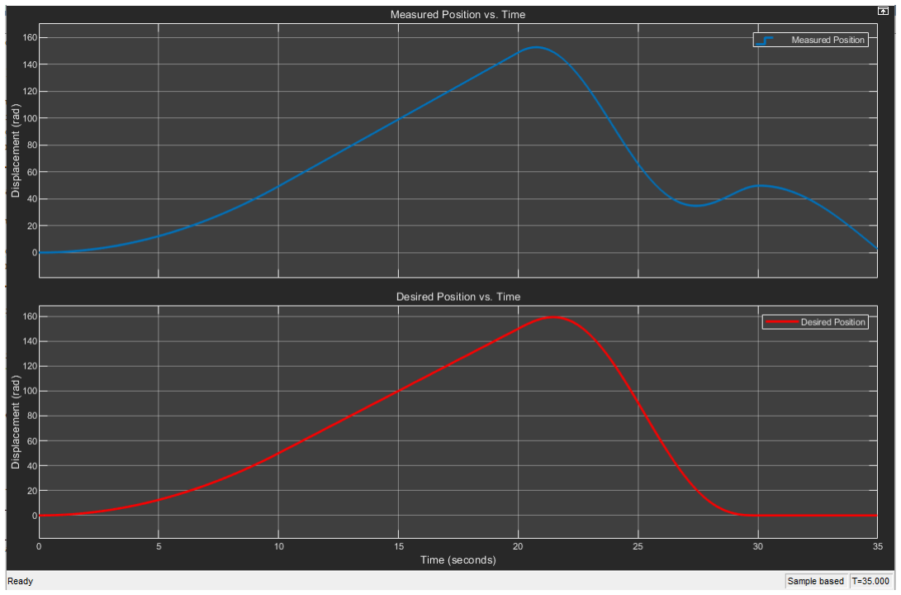
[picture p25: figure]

Figure 32: Closed-Loop Position Response

Figure 32 shows the closed-loop position response with desired kinematic profile. Based on the

discussions in Section 3 and Position Control section, regarding the bandwidth frequency of this

position loop being orders of magnitude lower than the inner speed loop, we tune the current

controller parameters as shown in Table 9.

Table 9: Position Loop controller gains.

Gain | Value
Kp | 2 ∗ π ∗ fs ∗ L ∗ (1/100),
Ki | 0.1
KD | 1

Where, (1/100) is used to reduce the bandwidth of the position controller by 10 times in

comparison to the inner speed and current loop and fs
is the sampling frequency used in the simulation. We set our sample time to be 1
4000

and this gave us smooth current, velocity, and

position plots.

The following performance evaluation Section 4.2 contains a detailed discussion of all three

controller blocks for both open-loop and closed-loop responses.

### 4.2. Performance Evaluation

In this section we analyze the plots shown for Open-loop and closed-loop responses of the

cascaded current, speed, and position controllers.

4.2.1. Open-Loop Analysis:

Table 10 summarizes the results of the open loop step response.

Table 10: Open Loop Analysis

Controller Block | Proportional Gain (Kp) | Integral Gain (Ki ) | Derivative Gain (Kd)
Current Control | 1 | 0 | 0
Speed Control | 1 | 0 | 0
Position Control | 1 | 0 | 0

Figures 27, 28, and 29 clearly show that the system response in open loop is unstable. For starters,

there is no correction factor, so the system response is abnormal.

When the desired and measured plots for all three figures are compared, we can see that the actual

plots are completely out of bounds in comparison to the desired ones. In Figure 27, the resultant

desired current value is so high that the motor is unable to generate it and is cutoff around 1.5A,

while the desired current continues to ramp up from 0 to 10 seconds. Due to the provided negative

acceleration, the desired current value drops to zero after 20 seconds of retraction, and the

measured current gives a negative spike at the instant and then drops to zero, resulting in the motor

shutting down.

The kinematic profile generates the desired angular speed for the motor, but because there is no

feedback to the speed controller, the motor behaves erratically, resulting in an exponential increase

in measured speed for the first 10 seconds. Because the desired speed is constant, the motor speed

goes to constant between 10 and 20 seconds; however, both constant values are different because the controller lacks a feedback loop. Because of the preceding reason, at retraction time, after 20

seconds of negative acceleration, the motor comes to a halt.

4.2.2. Closed-Loop Analysis:

Table 11 summarizes the results of the closed loop step response.

Table 11: Closed Loop Analysis

Controller Block | Proportional Gain (Kp) | Integral Gain (Ki ) | Derivative Gain (Kd)
Current Control | 2.808 | 259.8 | 0
Speed Control | 0.2808 | 0.0132 | 0.001
Position Control | 0.02808 | 0.1 | 1

To attain the desired outputs, based on our kinematic profile shown in Figure 25, a feedback loop

is used in each controller block to generate the plots shown in Figures 30, 31, and 32.

For the current control plot in Figure 30, the measured current ramps up proportionally to the

desired current for the first 10 seconds before becoming constant for the remaining 10 seconds.

The measured current closely resembles the desired current profile, with slight positive and

negative peaks and overshoots. The desired current peaks between 4 A and -8 A due to the negative

acceleration applied at 20 seconds, whereas the measured current peaks between 1 A and -2 A.

The controller prevents the motor from overshooting its values, making it more dynamically stable.

According to Figure 31, for the speed profile, the controller performs well for the first 20 seconds

(where angular speeds ramp and cruise), but there are undershoots between 20 and 30 seconds.

The measured speed lags the desired speed because of these undershoots, and to compensate for

this undershoot, the measured speed overshoots at 30 seconds and ramps down to zero, whereas

the desired speed goes to zero and remains at zero until 35 seconds (end of simulation). The

mechanical vibration and reluctance experienced by the inertial load when the motor shaft moves

in the opposite direction cause the undershoot.

According to Figure 32, the position controller responds to the system within the range of desired

input for the displacement profile. The measured position follows the desired position with

minimal error until the retraction time (i.e., 0 26 seconds) where negative acceleration is applied.

The measured position plot then begins to deviate from the desired position plot, but both

eventually return to zero at 35 seconds, when the simulation ends.

## 5. Conclusion

This report contains a detailed analysis and simulation of the electronics and control design for a

one-degree-of-freedom throwing arm. The primary purpose of this report was to integrate our

mechanical system with an electronic and control system.

We conducted an in-depth analysis of motor drive circuitry in the first section of this report. Three

motors were initially chosen, and their systematic behavior was compared to select the best one

for our throwing arm.

The motor we chose was the “GM8224S009”, and it was chosen based on the time it took to reach

its steady state value, the current required to generate torque, and the RPM required by the system.

Following the selection of the motor, three different cases were investigated to learn more about

the motor's behavior with/without heatsink and with different modes of simulation. After

simulating all these cases we made following conclusions:

1. In averaged mode system reaches steady state in less time than in PWM mode.
2. Every electronic component generates heat during operation; using a heat sink, which is one of the most effective methods for managing power dissipation, greatly reduces the risk of overheating.

The implementation of a control algorithm on the integrated system was the final part of this

project report. In this section, we began with a feedback loop for current control and progressed to

a cascade system with velocity and position control. Figure 25 depicts the desired profile for

current, position, and speed; these desired profiles served as our system's reference signals. We

used a PI and PID controller for our feedback control system, which we tuned after determining

the root locus of our desired poles. Despite minor differences, the tuned parameters were effective

in incorporating the desired inputs.

## 6. References

[1] H. DO, H. WORKS and I. Q, "[Explained] H-Bridge Circuit design, Applications,

Advantages", ETechnoG - Electrical, Electronics and Technology, 2021. [Online].

Available: https://www.etechnog.com/2019/03/h-bridge-circuit-working-application-

advantage.html (https://www.etechnog.com/2019/03/h-bridge-circuit-working-application-advantage.html)

[2] | P. | Jain, | "Current | Sensors", | Engineers | Garage, | 2021. | [Online]. | Available:

https://www.engineersgarage.com/current-sensors/.

[3] MSE-312 Lectures Mehrdad Moallem.
[4] Moog.com, 2021. [Online]. Available:

https://www.moog.com/content/dam/moog/literature/MCG/moc23series.pdf.

[5] "PC280LG-011 datasheet", Datasheetspdf.com, 2021. [Online]. Available:

https://datasheetspdf.com/pdf-file/1303801/JohnsonMotor/PC280LG-011/1.

[6] Servocomponents.com, 2021. [Online]. Available:

http://www.servocomponents.com/_literature_114806/GM8224S009_PDF.

## 7. Appendix A

### 7.1. Motor 1: GM8224S009 Datasheet

### 7.2. Motor 2: C23-L33 W10 Datasheet

### 7.3. Motor 3: PC280LG-011 Datasheet

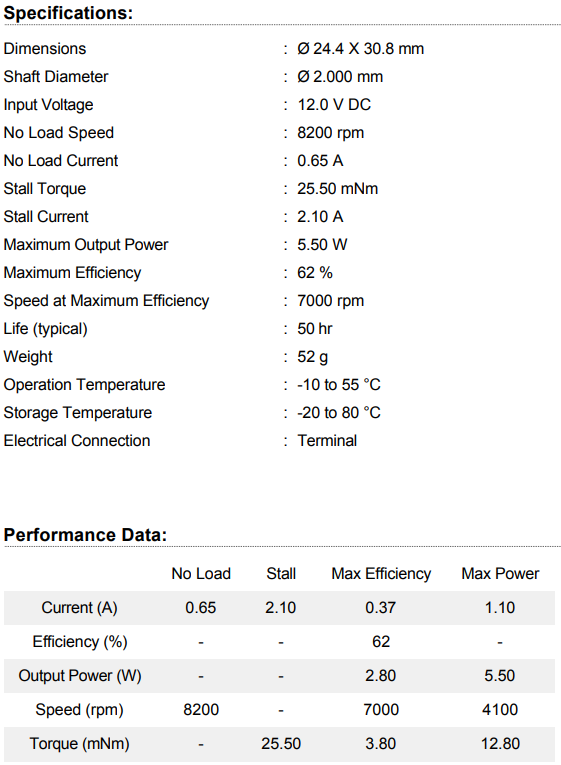
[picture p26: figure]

## 8. Appendix B

## 9. Appendix C

### 9.1. Electrical Model and Subsystems

### 9.2. Controller Model and Subsystems

### 9.3. Position Controller Subsystem

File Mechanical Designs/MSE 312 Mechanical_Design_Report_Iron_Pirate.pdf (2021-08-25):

# MSE312


### MECHANICAL DESIGN AND ANALYSIS REPORT

Student Name | Student ID
Abdullah Tariq | 301297687
Junaid Jawed Khan | 301308300
Syed Imad Azeem Rizvi | 301297227

## Report due date: 21st June 2021

## Prepared for: Dr. Carolyn Sparrey

MSE-312 / MECHATRONIC DESIGN - II

MECHATRONIC SYSTEMS ENGINEERING

SCHOOL OF APPLIED SCIENCE

SIMON FRASER UNIVERSITY

## Table of Contents

## Introduction

In this project, we’re tasked with designing a one-degree of freedom arm that will produce a projectile motion using a regulation lacrosse ball to reach three targets. One-Degree of freedom robots are used in many different applications such as welding, manufacturing, pick and place etc. Based on our research, the most common solution to a one-degree of freedom (rotation) arm was a catapult with counterweight to produce the torque for the projectile motion. However, we don’t need a counterweight for torque generation, instead we have the option of selecting our own motor. Another existing design solution we found was a slingshot used to create the projectile motion by stretching the elastic band using a motor - this design had position sensors and the control algorithm was too complex to implement in the given time frame for our course. Given the limited time and resources, the team chose three structures that we believed can be easily validated and manufactured.

## Design Approach

The team unanimously agreed to follow the Human Centered Design theory. The general idea was to clearly identify our requirements, propose a solution that we believe would meet the requirements and analysis the solution using FEA and Simscape Multi-body. If the proposed design did not fail under the loading conditions applied, the proposed design was analyzed for its dynamic characteristics using Simscape Multi-body. If a proposed solution fails FEA analysis, the point of failure was improved and FEA was repeated. The improvements to the model were such that the model could still be manufactured within the given budget. This process was used by the team to design the mechanical structure that could produce the projectile motion while adhering to the given design constraints.

## Design Specifications

The design specifications to meet the functional requirements of mechanical structure are as follows:

- The designed structure should not fail due to cyclic loading requirements for projectile motion.
- The designed structure must have a vertical plane operation of 30 cm and should fit in a dome 10 cm wide.
- The designed structure must have a passive mechanism to hold and release a regulation lacrosse ball of 145g and 63mm diameter.
- The designed structure must minimize radial and axial forces on the shaft of the motor.
- The designed structure should be stiff enough to minimize deflection due to rapid acceleration produced by the motor.
- The designed structure should be easily rotated by a motor.

## Contributions

Team Member | Contributions
Syed Imad Azeem Rizvi | Worked on simscape and solidworks modelling of each design - including FEA
Abdullah Tariq | Worked on FEA and simscape modelling & analysis of each design
Junaid Jawed Khan | Worked on documentation, hand calculations of Design 1 and assisted with simscape troubleshooting.

## Analytical Analysis

In this section we present our hand calculation results for static and dynamic characteristics of our

three designs. These results are used for validating the FEA and Simscape simulation results.

### Design 1

The first arm structure is a simple hollow beam pinned at one end and a ball-holder on the free end as shown in figure 1.


Figure 1: Design 1 SolidWorks Model

The loads considered in the static analysis include the weight of the regulation size lacrosse ball and gravity.

Statics

For our static analysis of Design 1, we were interested in minimizing deflection on the free end. The geometry of the beam and boundary conditions were fixed. Therefore, to analyze deflection, we used different materials to minimize the deflection on the free end, making it easier for controlling the arm.

The three different materials we used were 1023 Carbon Steel, Titanium alloy (Cp-Ti UNS R50400) and Brass. The justification for these materials is provided in the Material Selection section of this report.

Figure 2 is the Free Body diagram used for statics hand-calculations.


Figure 2: Statics Analysis Free Body Diagram.

The hand calculations are used for validation of FEA of Design 1. The equation used for populating the following table are included Appendix A under Statics. The results are tabulated as shown table 1.

Table 1: Static Analytical Results of Design 1

Fatigue Stress Limit (N/mm^2) | Maximum Stress (N/mm2) | Deflection (mm)
1023 Carbon Steel | 255 | 1.989e+01 | 0.980
Cp-Ti UNS R50400 | 291 | 1.245e+01 | 1.298
Brass | 216 | 2.250e+01 | 1.879

Based on the analytical results shown in Table 1, using Brass as the material for the arm results in

the greatest deflection. Moreover, using Brass results in a greater stress in comparison to the other

materials.

Dynamics

For our kinematic analysis of Design 1, we were interested in minimizing the mass moment of inertia of the structure to reduce the torque needed from the motor to rotate the arm. Since the mass distribution and location of the axis of rotation is fixed for our structure, different choices of material were used to change the total mass moment of inertia of the structure.

Figure 3 is the Free Body diagram used for dynamics hand-calculations.


Figure 3: Kinematic Analysis Free Body Diagram

The hand calculations are used for validation of Simscape simulation of Design 1. The equation used for populating the following table are included Appendix A under Dynamics. The results are tabulated as shown in Table 2.

Table 2: Kinematic Analytical Results of Design 1

Total Mass Moment of Inertia | Angular Velocity (rad/sec) | Angular Acceleration (rad/sec² )
1023 Carbon Steel | 0.03379290 | 14.89 | 98.78
Cp-Ti UNS R50400 | 0.00127061 | 18.69 | 143.43
Brass | 0.03655379 | 13.27 | 94.14

Based on the analytical results shown in Table 2, using the Titanium alloy for the arm structure produced the largest angular velocity and acceleration. This was because the Titanium alloy has the lowest density (ρ = 4510 kg
m³

) in comparison to the other materials (1023 Carbon Steel ρ = 7858 kg
m³

, and Brass ρ = 8500 kg
m³

) [1][2][3].

### Design 2

The second design for creating a projectile motion is to launch a ball from an inclined base. The ball initially rests an elevation, followed by rolling down the track and getting projected by pair of flywheels connected to the motor. Figure 4 shows the SolidWorks model for this design.


Figure 4: Design 2 – SolidWorks Model

Inspiration of this design is taken from the tennis ball launcher, that uses a similar mechanism of two combination of wheels that rotates opposite with respect to each other and launches the ball forward when passed through them. It can be observed from the figure that, the assembly constitutes of a combination of 4 gears required to produce a desired motion with the addition to the red color shaft that is driven by the motor. The gap between the two wheels is the optimum distance that is required to being in contact with the ball, compressing it a bit, but the ball remains in its elastic deformation.

Statics

The slide is fixed with a rigid support structure. The free body diagram in figure 5 shows the reaction forces, weight of the ball and bending moment that will be produced when the boll rolls down on the track. An assumption has been made, that the ball weight is evenly distributed on the slide when it is in contact with it. The slide is solid in its geometry, and its slope is assumed to be a straight line rather than being curved.


Figure 5: Free body diagram of track

The hand calculations are used for validation of FEA of Design 2. The equation used for populating the following table are included Appendix B under Statics. The results are tabulated as shown table 3.

Table 3: Statics Analytical Results of Design 2

Fatigue Stress Limit (N/mm^2) | Maximum Stress (N/mm2) | Deflection (mm)
1023 Carbon Steel | 255 | 1.436e-01 | 2.823e-04
Cp-Ti UNS R50400 | 291 | 0.926e-01 | 3.528e-04
Brass | 216 | 1.362e-01 | 5.646e-04

Dynamics

Figure 6 shows the free body diagram of the ball when it is in motion.


Figure 6: Free body diagram of ball's motion.

A few assumptions have been made to ease with the calculations and simulations. The ball rolls on the track throughout its motion, and it never slips or skids. The contact frictional forces have been considered for frictional losses and its coefficient changes with the material. The slide has been broken down into three parts to simplify the calculation. The ball has a fixed gravitational potential energy at the beginning, that is transferred into both rotational and translational kinetic energy with frictional losses just before reaching the rotating fly wheels. It is assumed that there is no deformation taking place when the ball passes through the wheels. The ball then launches at an angle of 45º degree to achieve maximum distance.

The hand calculations are used for validation of Simscape simulation of Design 2. The equation used for populating the following table are included Appendix B under Dynamics. The results are tabulated as shown in Table 4.

Table 4: Kinematics Analytical Results of Design 2

Angular Velocity (rad/sec) | Angular Acceleration (rad/sec² )
1023 Carbon Steel | 165.671 | 2.420
Cp-Ti UNS R50400 | 162.14 | 2.613
Brass | 144.83 | 2.1175

### Design 3

The third design for creating a projectile motion is to launch the ball using a spring mechanism. Figure 5 shows the SolidWorks model for this design.


Figure 7: Design 3 SolidWorks Model

This design uses a similar idea of a gun firing a bullet. A cork shaped bullet is screwed down to a spring (fixed on one end of the gun), and the bullet is tied down to a shaft, by a non-flexible string as shown above.

Statics

Figure 8 shows the free body diagram for the gun.


Figure 8: Free body diagram of gun.

As it can be observed in figure 5 there is a hemispherical opening for the ball that is placed on the gun elevated at a 45º angle. The ball is assumed to be exerting an evenly distributed force (i.e., its weight) at the lower half of the hemispherical opening of the gun. It is assumed that the gun has a uniform distribution, where its center of mass is concentrated at its geometrical center. The reaction forces then act on the gun at its pillars, and their sum is evenly distributed on its cylindrical part of contact. This helps balance the weight of the gun as well as the ball.

The hand calculations are used for validation of FEA of Design 3. The equation used for populating the following table are included Appendix C under Statics. The results are tabulated as shown table 5.

Table 5: Statics Analytical Results of Design 3

Fatigue Stress Limit (N/mm^2) | Maximum Stress (N/mm2) | Deflection (mm)
1023 Carbon Steel | 255 | 1.151e-01 | 1.983e-04
Cp-Ti UNS R50400 | 291 | 8.277e-02 | 2.783e-04
Brass | 216 | 1.042e-01 | 3.868e-04

Dynamics

Figure 9 shows the free body diagram used for dynamic analysis of Design 3.


Figure 9: Free body diagram of ball's motion.

From figure 9 it can be observed that when the shafts rotate, its angular displacement (i.e., the arc length) is equal to the linear displacement of the string when the string wraps around the shaft. We assume that the string compresses the spring sufficiently to store the elastic potential energy in it. When the input from the motor shaft is stopped, the shafts rotate freely, and the spring is relaxed. The spring when released generates a force required to hit the ball giving it the desired initial velocity to reach the given target.

The hand calculations are used for validation of Simscape simulation of Design 3. The equation used for populating the following table are included Appendix C under Dynamics. The results are tabulated as shown in Table 6.

Table 6: Kinematics Analytical Results of Design 3

Angular Velocity (rad/sec) | Angular Acceleration (rad/sec² )
1023 Carbon Steel | 1049.22 | 18.426
Cp-Ti UNS R50400 | 775.62 | 20.896
Brass | 916.11 | 16.206

## Qualitative Analysis

In this section the results of FEA and Simscape simulation for each design are presented. The sensitivity of each design to different materials and mesh size was observed. Moreover, the dynamic sensitivity of each design was studied by creating a simulation in Simscape.

The three different materials used for FEA study and Simscape simulation have different densities. One of our design objectives is to ensure the arm structure does not fail under cyclic loading and has minimal deflection. The three materials studied are 1023 Carbon Steel (ρ = 7858 kg
m³

), Cp-Ti
UNS R50400 (ρ = 4510 kg
m³

), and Brass (ρ = 8500 kg
m³

) [1][2][3].

### FEA Results

In this section we have tabulated all our FEA results for each design. The results are compared

with the analytical values in the Validation section.

Design 1
Table 7: FEA of Design 1
Coarse Mesh | Fine Mesh
Deflection (mm) | Maximum Stress (N/mm2) | Time Taken (s) | Deflection (mm) | Maximum Stress (N/mm2) | Time Taken (s)
1023 Carbon Steel | 1.067 | 2.459e+01 | 01 | 7.961e-01 | 2.012e+01 | 08
Cp-Ti UNS R50400 | 1.418 | 1.708e+01 | 01 | 8.908e-01 | 1.212e+01 | 08
Brass | 2.317 | 2.634e+01 | 01 | 1.764 | 2.226e+01 | 08

Design 2
Table 8: FEA of Design 2
Coarse Mesh | Fine Mesh
Deflection (mm) | Maximum Stress (N/mm2) | Time Taken (s) | Deflection (mm) | Maximum Stress (N/mm2) | Time Taken (s)
1023 Carbon Steel | 3.257e-04 | 1.62e-01 | 01 | 4.186e-04 | 2.564e-01 | 05
Cp-Ti UNS R50400 | 3.878e-04 | 1.003e-01 | 01 | 5.086e-04 | 1.616e-01 | 06
Brass | 7.139e-04 | 1.723e-01 | 01 | 9.232e-04 | 2.751e-01 | 06

Design 3
Table 9: FEA of Design 3
Coarse Mesh | Fine Mesh
Deflection (mm) | Maximum Stress (N/mm2) | Time Taken (s) | Deflection (mm) | Maximum Stress (N/mm2) | Time Taken (s)
1023 Carbon Steel | 2.359e-04 | 1.318e-01 | 01 | 2.624e-04 | 2.216e-01 | 03
Cp-Ti UNS R50400 | 2.999e-04 | 8.587e-02 | 01 | 3.374e-04 | 1.413e-01 | 03
Brass | 5.084e-04 | 1.393e-01 | 01 | 5.672e-04 | 2.351e-01 | 04

### Simscape Results

In this section we studied the dynamic characteristics of each design. For each design we started the simulation with a base model, followed by changing each base model property and observing its effect on the angular velocity and acceleration.

Design 1

The base model configuration for design 1 is as follows. The arm material was set to 1023 Carbon Steel (ρ = 7858 kg
m³

), initial torque from a virtual motor was set to 5 Nm, the damping coefficient was set to 1e-4, and we used auto ode45 solver to carry out the base model simulation [2].

Table 10 shows the dynamic sensitivity analysis results of Design 1.

Table 10: Simulation Results of Design 1

| Angular Velocity (rad/sec) | Angular Acceleration (rad/sec² )
Base model | 15.46 | 101
Material Titanium | 19.562 | 146
Material Brass | 15.14 | 96.3
Solver (ode15s / step time 0.001s) | 15.793 | 102
Damping (1e-1) | 0.589 | 0.152
Torque (50 Nm) | 54.088 | 1008.933

Based on the results shown in Table 10, the angular acceleration for the base model was high because the base material required more torque to rotate the arm from the rest position. The change in material of the rotating increased the angular velocity achieved for Titanium because its density is almost half that of both Carbon Steel and Brass. Therefore, for the same torque it achieved a higher angular velocity. Using a different solver for the base model did not have any significantly effect on the angular velocity and acceleration. Damping the base model had a significant impact on Design 1 as the initial torque wasn’t enough to lift the shaft from its resting position at 0 degrees. Increasing the torque by ten times provided a greater moment and this led an increase in angular velocity and acceleration for the base model.

Design 2

The base model configuration for design 2 is as follows. The slide material was set to 1023 Carbon Steel (ρ = 7858 kg
m³

) and the gears were given a fixed density of 500 kg
m³

, initial torque from a
virtual motor was set to 1 Nm, the damping coefficient was set to 1e-4, and we used auto ode45 solver to carry out the base model simulation [2].

Table 11 shows the dynamic sensitivity analysis results of Design 1.

Table 11: Simulation Results of Design 2

| Angular Velocity (rad/sec) | Angular Acceleration (rad/sec² )
Base model | 174.391 | 1206
Material Titanium | 174.34 | 834
Material Brass | 174.498 | 1131
Solver (ode15s / step time 0.001s) | 174.533 | -1.3e-1
Damping (4e-5) | 436 | 1000
Torque (0.01 Nm) | 1.744 | 12.8

Based on the results shown in Table 11, we noticed that the angular velocity didn’t change significantly when changing the materials of the base model. As we know from previous design analysis that densities of Carbon Steel, and Brass are close, which explains the similarity in angular velocity and acceleration. The angular acceleration needed to achieve the same angular velocity with Titanium was lower in comparison to base model because in comparison to Carbon Steel its density is almost half. Hence, titanium structure would require less torque to achieve the same angular velocity in comparison to a denser material. Reducing damping of the base model increased the angular velocity achieved as less input energy was dissipated.

Design 3

The base model configuration for design 3 is as follows. The spring material was set to 1023 Carbon Steel (ρ = 7858 kg
m³

) and the bullet was given a fixed density of 500 kg
m³

, initial force
derived from a virtual motor torque was set to 4 N, the damping coefficient was set to 1e-8, and we used auto ode45 solver to carry out the base model simulation [2].

Table 12 shows the dynamic sensitivity analysis results of Design 3.

Table 12: Simulation Results of Design 3

| Angular Velocity (rad/sec) | Angular Acceleration (rad/sec² )
Base model | 2.751 | 22.2
Material Titanium | 2.751 | 22.2
Material Brass | 2.751 | 22.2
Solver (ode15s / step time 0.001s) | 2.751 | 22.2
Damping (1e-1) | 2.634 | 20.17
Force (40 N) | 33.92 | 271.3

Based on the results shown in Table 12, simulating the model with the initial configuration produced the shown angular velocity and acceleration. As our third design mechanism is strongly depended on spring contraction and expansion, we provided planar joint with a certain force to attain our desired torque in Simscape. As the joint is located after spring and bullet, changing their materials did not have any effect on the simulation result. Same conclusions were drawn when using two different solvers. Damping affect was also minimal in this design as after increasing damping coefficient to 1e-1 from 1e-8 angular velocity value only decreased by 0.12 while angular acceleration drooped to 20.17. This minimal affect was seen because force was acting on the joint just behind the ball so damping property for the parts connected behind that point did not have any effect. Lastly simulation results were obtained by increasing the torque to 40Nm. As expected, angular velocity and angular acceleration increased significantly in comparison to the base model.

## Validation

### Statics (SolidWorks)

Table 13: Qualitative vs Analytical Comparison of Statics

| Maximum Stress
Design 1 | Design 2 | Design 3
Material | Analytical | FEA | Analytical | FEA | Analytical | FEA
Carbon Steel | 1.989e+01 | 2.459e+01 | 1.436e-01 | 1.62e-01 | 1.151e-01 | 1.318e-01
Titanium | 1.245e+01 | 1.708e+01 | 0.926e-01 | 1.003e-01 | 8.277e-02 | 8.587e-02
Brass | 2.250e+01 | 2.634e+01 | 1.362e-01 | 1.723e-01 | 1.042e-01 | 1.393e-01
| Deflection
Design 1 | Design 2 | Design 3
Material | Analytical | FEA | Analytical | FEA | Analytical | FEA
Carbon Steel | 0.980 | 1.067 | 2.823e-04 | 3.257e-04 | 1.983e-04 | 2.359e-04
Titanium | 1.298 | 1.418 | 3.528e-04 | 3.878e-04 | 2.783e-04 | 2.999e-04
Brass | 1.879 | 2.317 | 5.646e-04 | 7.139e-04 | 3.868e-04 | 5.084e-04

Based on the qualitative and analytical comparisons shown in Table 13, we can note that the maximum stress and deflection of all each design’s hand calculations are not exact but are within an acceptable degree of error. So, we’re certain that based on our assumptions mentioned in the analytical section FEA studies are acceptable.

### Kinematics (Simscape)

Table 14: Qualitative vs Analytical Comparison of Kinematics

| Angular Velocity
Design 1 | Design 2 | Design 3
Material | Analytical | Simulation | Analytical | Simulation | Analytical | Simulation
Carbon Steel | 14.89 | 15.46 | 165.671 | 174.391 | 1049.22 | 1206
Titanium | 18.69 | 19.562 | 162.14 | 174.34 | 775.62 | 834
Brass | 13.27 | 15.14 | 144.83 | 174.498 | 916.11 | 1131
| Angular Acceleration
Design 1 | Design 2 | Design 3
Material | Analytical | Simulation | Analytical | Simulation | Analytical | Simulation
Carbon Steel | 98.78 | 101 | 2.420 | 2.751 | 18.426 | 22.2

Titanium | 143.43 | 146 | 2.613 | 2.751 | 20.896 | 22.2
Brass | 94.14 | 96.3 | 2.1175 | 2.751 | 16.206 | 22.2

Based on the qualitative and analytical comparisons shown in Table 14, we can note that the angular velocity and acceleration of all each design’s hand calculations are not exact but are within an acceptable degree of error. So, we’re certain that based on our assumptions mentioned in the analytical section we’ve modelled our designs correctly.

## Design Evaluations

This section evaluates the three proposed designs for the mechanical structure based on the results presented in the analysis sections. The evaluation was carried out using a decision matrix. The template of the decision matrix is as shown below.

Structure | Design #
Objective | Weight | Score | Weight*Score

The objectives of the mechanical structure were assigned a weight between 1-5 and based on the results found in the analysis sections, a score was assigned to each design. The largest overall score is the optimal design to meet the design specifications.

### Decision Matrix

Table 15 is the decision matrix constructed to select the optimal design.

Table 15: Design Evaluation Matrix

Structure | Design 1 | Design 2 | Design 3
Moment of Inertia | 5 | 3 | 15 | 4 | 20 | 5 | 25
Volume (Cost) | 5 | 1 | 5 | 5 | 25 | 3 | 15
Deflection | 4 | 1 | 4 | 3 | 15 | 4 | 16
Maximum Stress | 4 | 1 | 4 | 3 | 12 | 5 | 20
Overall Value | | 28 | | 72 | | 76

Based on Table 14, Design 3 provided the highest angular velocity for each material. Therefore, Design 3 was given the highest score as it provided the minimal moment of inertia - a design requirement.

To minimize the cost of manufacturing the selected design, volume was taken into consideration in the decision matrix. The volumes of Design 1, 2 and 3 are 0.00277246603, 0.00112849786, 0.0014241914 cubic meters, respectively. Design 1 would cost the most and Design 2 would cost the least, which is reflected by the scores given.

Based on Table 13, Design 1 has the highest deflection and stress, and Design 3 has the lowest. Therefore, Design 3 was given the highest score and Design 1 was given the lowest score.

The overall score shows that Design 3 is the optimal design that meets the design specifications that were laid out at the start of this documentation.

### Material Selection

In this section we compare the stiffness, strength, processability and availability properties of the three materials used in the analysis sections of this report to select the optimal material for our final design. The three properties are used for comparison because they help us achieve our design specifications.

The following decision matrix was constructed to assist the optimal choice. Each material is scored from 0-5 for each property.

Decision Matrix

Table 16: Material Selection Decision Matrix

Material Property | Cp-Ti UNS R50400 | 1023 Carbon Steel | Brass
Stiffness | 3 | 5 | 2
Strength | 5 | 3 | 1
Processibility | 2 | 4 | 2
Availability | 3 | 0 | 5
Overall Value | 13 | 12 | 10

The scores assigned to each material are justified as shown below:

- The Elastic Modulus of Cp-Ti UNS R50400, 1023 Carbon Steel, Brass is 120 GPa, 210 GPa, and 117 GPa respectively [1][2][3]. 1023 Carbon Steel can help us reduce deflection as it is relatively stiffer.
- The Tensile Strength of Cp-Ti UNS R50400, 1023 Carbon Steel, Brass is 485 MPa, 425 GPa, and 360 MPa respectively [1][2][3]. A stronger material will provide a greater safety factor for our cyclic loading application. Hence, Cp-Ti UNS R50400 is desired as it relatively stronger.
- The Machinability Index of Cp-Ti UNS R50400, 1023 Carbon Steel, Brass is 40, 65 and 40 respectively [3][4][5]. A lower machinability index means the cost of processing the material would be high as it would require more effort. Therefore, 1023 Carbon Steel is the best option in terms of processability.

- The availability score was given by taking our $550 budget into consideration. The 1023 Carbon Steel would require importing a ton from China which would cost us more than the available budget [6]. The Titanium alloy and brass are available within Canada from local vendors [7][8].

Based on the overall score, we have concluded that the Titanium alloy is the optimal choice of material for our final design as it will help us minimize deflection in our final design and is affordable.

## Bill of Materials

The allocated budget for this project is $550 CAD. For processing our Design 3, we will be taking advantage of MSE’s Lab Services. The following table lists all the expense of designing our selected design using the Titanium alloy.

Table 17: Bill of Materials and Services [7][9].

Component | Cost ($ CAD) | Supplier
Machining Services (Drilling & Cutting) | 30.00/ hour | SFU Services & Training
Cost of Titanium alloy | 22.34 /Kg | Aesteiron Steels

The selected design has a volume of 0.0014241914 cubic meters. Using the titanium alloy (ρ = 4510 kg
m³

) as our choice of material, the total mass is 6.42 Kg. Therefore, the total cost of the material is $143 CAD. According to our experience with the Machining services of SFU, we believe our design can be manufactured in three hours. Therefore, the total cost of manufacturing our selected design is $223 CAD. We still have $327 CAD to select our motor and circuit components to build a working prototype.

## Final Design Drawing


## References

[1]"Grade 2 Unalloyed Ti ("Pure") 50A (UNS R50400)", AZoM.com, 2021. [Online]. Available: https://www.azom.com/article.aspx?ArticleID=9413. [Accessed: 21- Jun- 2021].

[2]"AISI 1023 Carbon Steel (UNS G10230)", AZoM.com, 2021. [Online]. Available: https://www.azom.com/article.aspx?ArticleID=6524. [Accessed: 21- Jun- 2021].

[3]"Brass | UNS | C28000", AZoM.com, | 2021. | [Online]. | Available:
https://www.azom.com/article.aspx?ArticleID=6380. [Accessed: 21- Jun- 2021].

[4]"Machinability of Titanium - Machining Doctor", Machining Doctor, 2021. [Online]. Available: https://www.machiningdoctor.com/machinability/titanium/. [Accessed: 21-Jun- 2021].

[5]1. Low-Carbon Steels 1022, "Low-Carbon Steels 1022, 1023, 1025 and 1026", All Metals & Forge Group, 2021. [Online]. Available: https://steelforge.com/carbon-steel-1022/. [Accessed: 21- Jun- 2021].

[6]"1023 Carbon Mild Steel Sheet and Plates - Buy Hot Rolled Steel Plate, Ar500 Steel Plate, Carbon Steel Plate Product on Alibaba.com", Alibaba.com, 2021. [Online]. Available: https://www.alibaba.com/product-detail/1023-Carbon-Steel-Per-Sheet-1023_1600137686909.html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. [Accessed: 21- Jun- 2021].

[7]"Titanium distributor and supplier/ Grade 2/ 5 Price per kg", Aesteiron.com, 2021. [Online]. Available: https://www.aesteiron.com/titanium.html. [Accessed: 21- Jun- 2021].

[8]"Scrap Metal Prices | Canada – All of the latest scrap metal prices in
Canada.", Scrapmetalpricer.ca, 2021. [Online]. Available: https://www.scrapmetalpricer.ca/. [Accessed: 21- Jun- 2021].

[9]"Rates & Equipment List - Mechatronic Systems Engineering - Simon Fraser University", Sfu.ca, 2021. [Online]. Available: https://www.sfu.ca/mechatronics/services-and-training/rates-and-equipment-list.html. [Accessed: 21- Jun- 2021].

## Appendix A

### Design 1

Statics


Kinematics


FEA Study Sample

Simscape Model

## Appendix B

### Design 2

Statics


Dynamics


FEA Study Sample

Simscape Model

## Appendix C

### Design 3

Statics


Dynamics


FEA Study Sample


Simscape Model


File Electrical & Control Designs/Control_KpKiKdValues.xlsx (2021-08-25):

FULL SYSTEM | Current Control |  |  | Speed Control |  |  | Position Control
 | Kp | Ki | Kd | Kp | Ki | Kd | Kp | Ki | Kd
 | 29.302096 | 35.555278 | 0 | 2.92346 | 6.589961

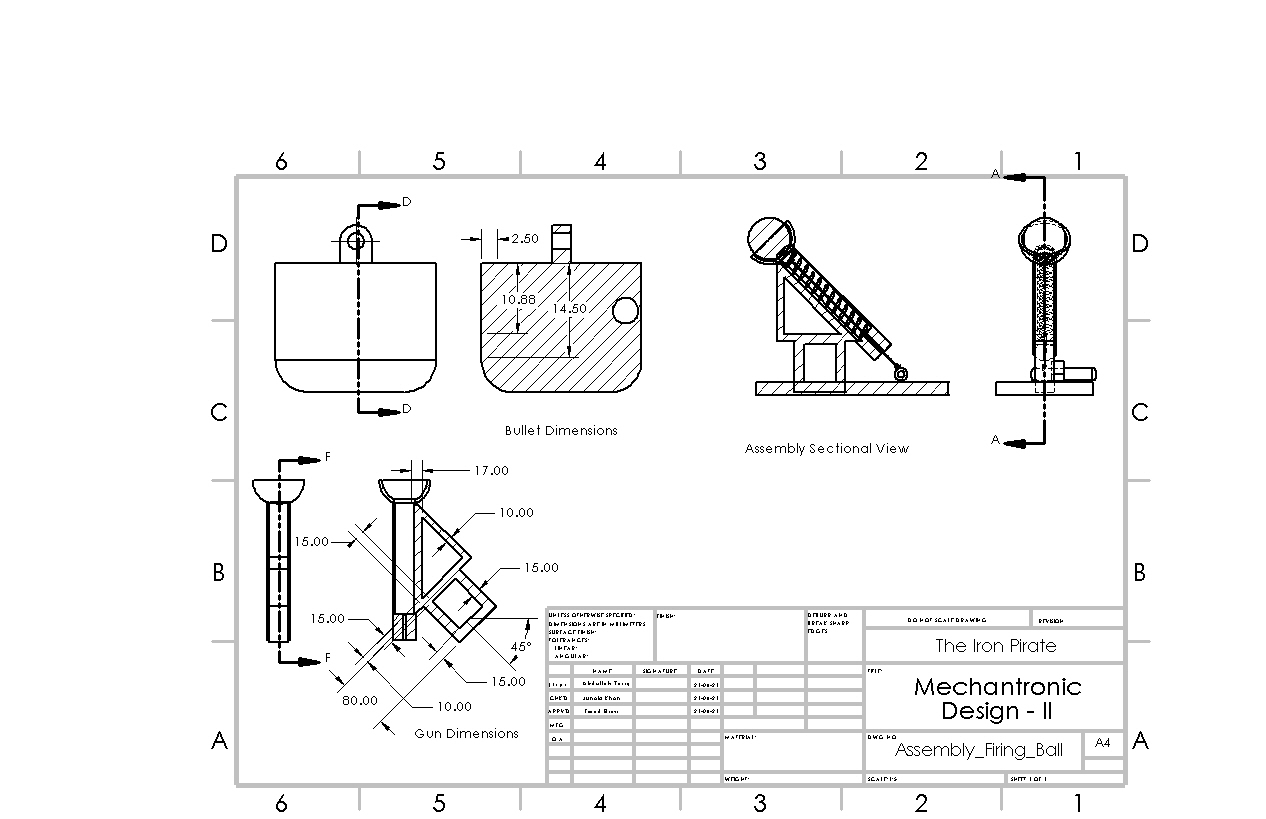
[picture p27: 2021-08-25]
Mechanical Designs/Engineering_Drawing.JPG

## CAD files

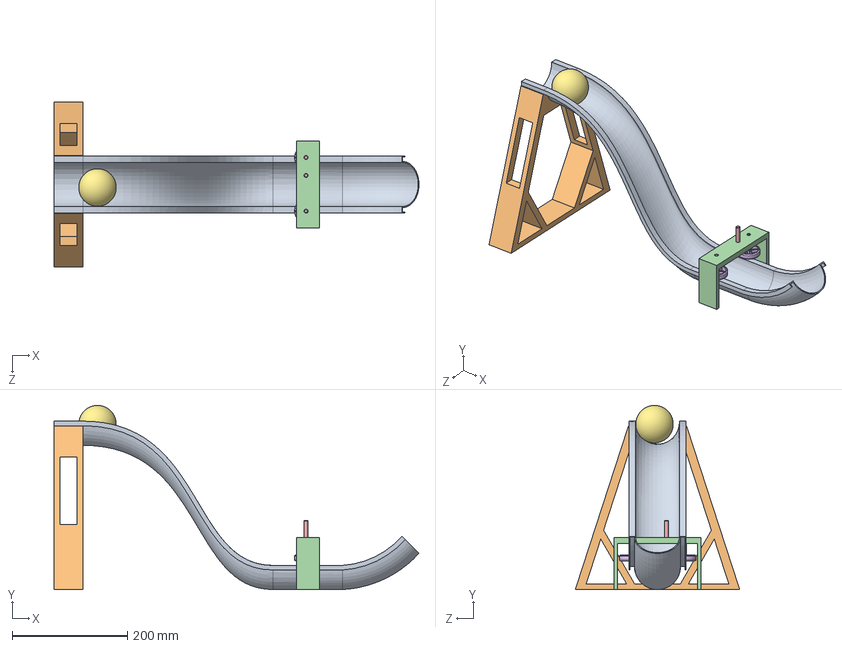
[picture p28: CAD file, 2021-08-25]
Mechanical Designs/Fly Wheel/SolidWorks/Assembly_Fly_Wheel.SLDASM
632.8 x 319.4 x 285.2 mm
Slide
Support1
spur gear_iso x 4
Housing
Shaft x 3
Wheel x 2
Ball

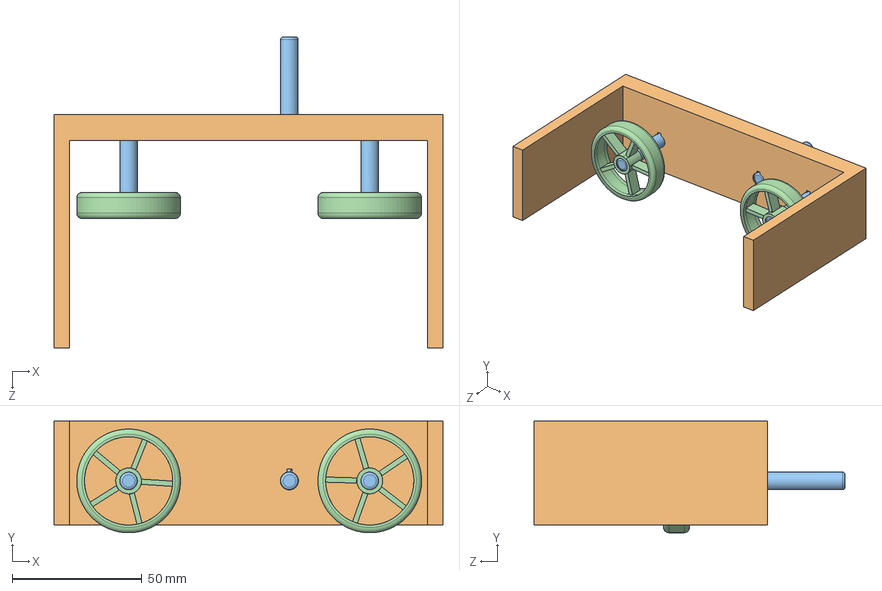
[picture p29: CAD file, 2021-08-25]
Mechanical Designs/Fly Wheel/SolidWorks/Gear_Box.SLDASM
150.0 x 43.0 x 120.0 mm
spur gear_iso x 4
Housing
Shaft x 3
Wheel x 2

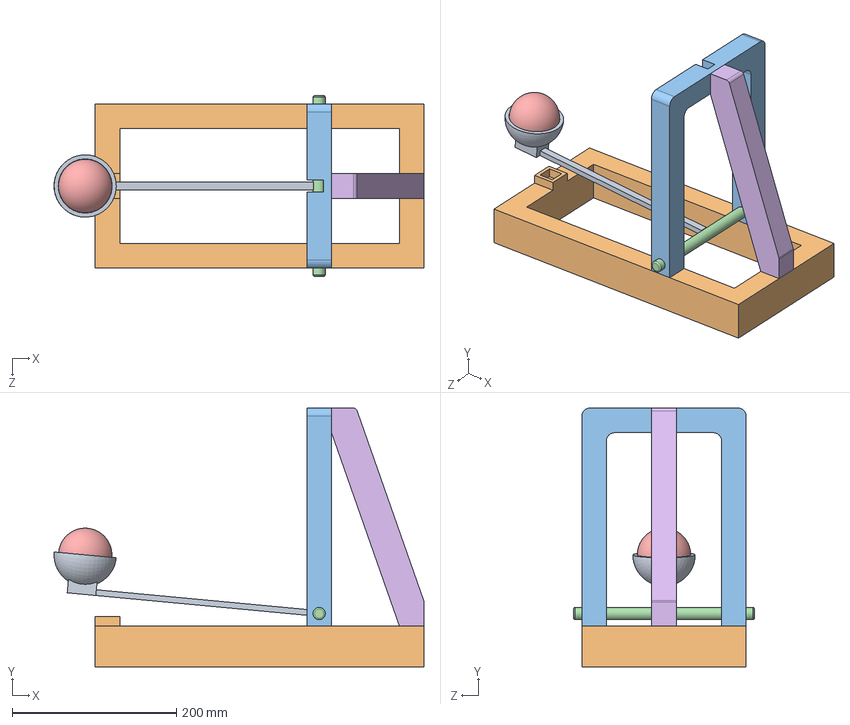
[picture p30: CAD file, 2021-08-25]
Mechanical Designs/Throwing Arm/SolidWorks/Assembly_Throwing_Arm.SLDASM
450.0 x 315.0 x 220.0 mm
Arm
Base
Frame
Shaft
Ball
Support_TA

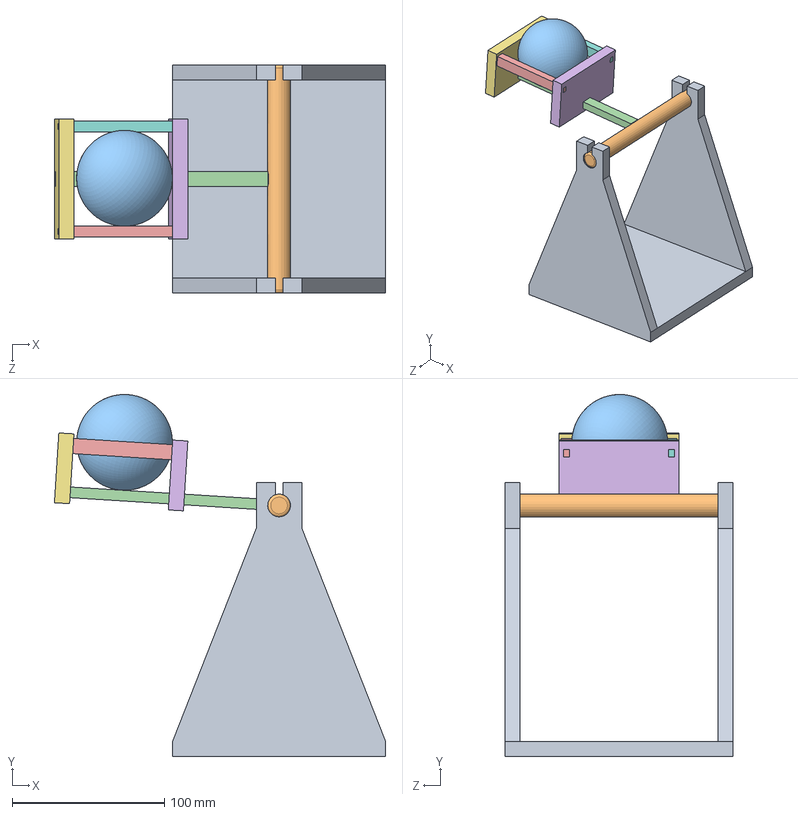
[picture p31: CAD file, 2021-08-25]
Mechanical Designs/Throwing_Arm_Modified/Assembly_Throwing_Arm.SLDASM
217.7 x 237.9 x 150.0 mm
Base
Shaft
Ball
Beam
Support_E
Support_N
Support_S
Support_W

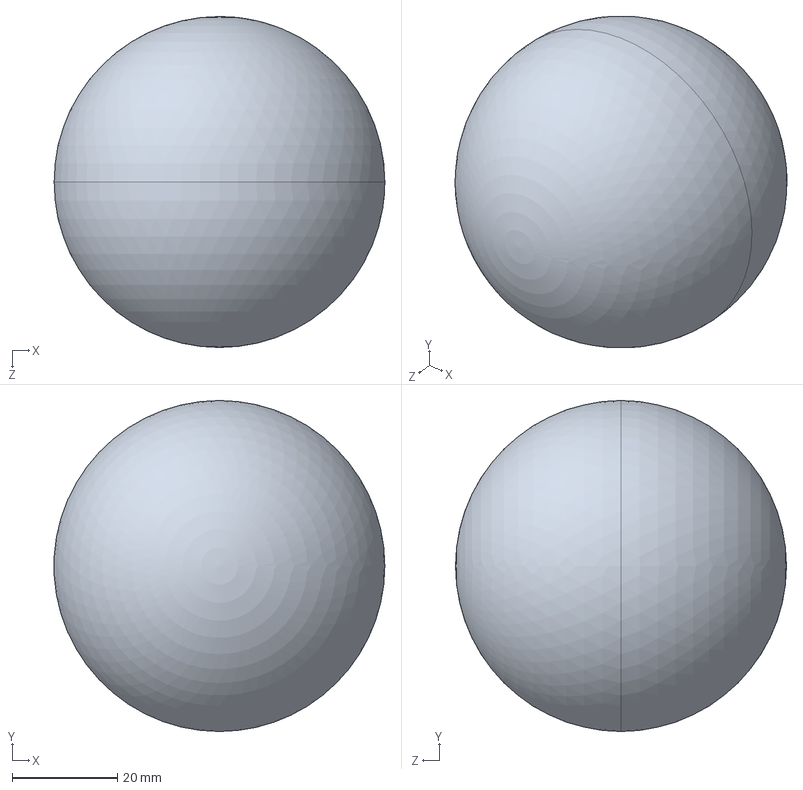
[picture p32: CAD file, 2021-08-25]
Integration/Throwing Arm Modified/Ball.STEP
62.9 x 63.0 x 63.0 mm

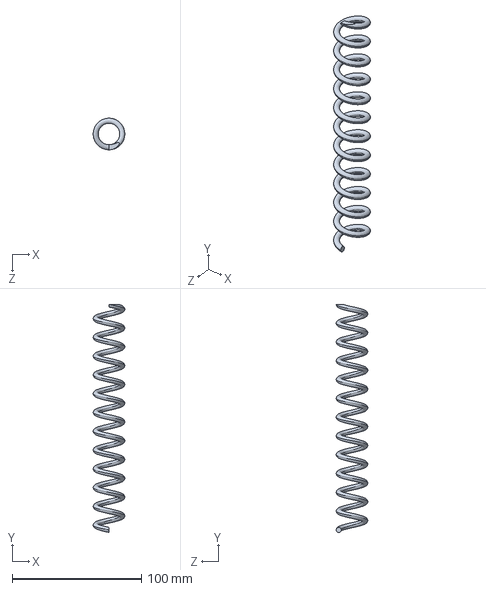
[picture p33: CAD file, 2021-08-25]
Mechanical Designs/Firing Ball/Simscape/Spring_Default_sldprt.STEP
24.5 x 176.4 x 24.5 mm

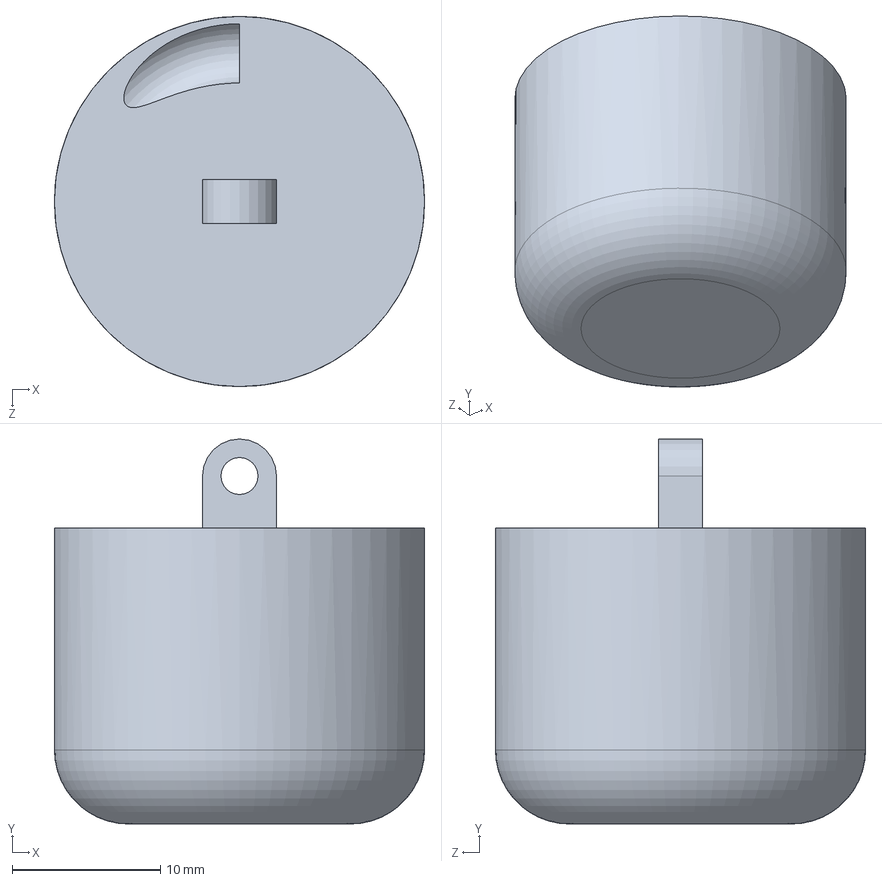
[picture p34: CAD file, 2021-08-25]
Mechanical Designs/Firing Ball/SolidWorks/Bullet.SLDPRT
25.0 x 26.0 x 25.0 mm

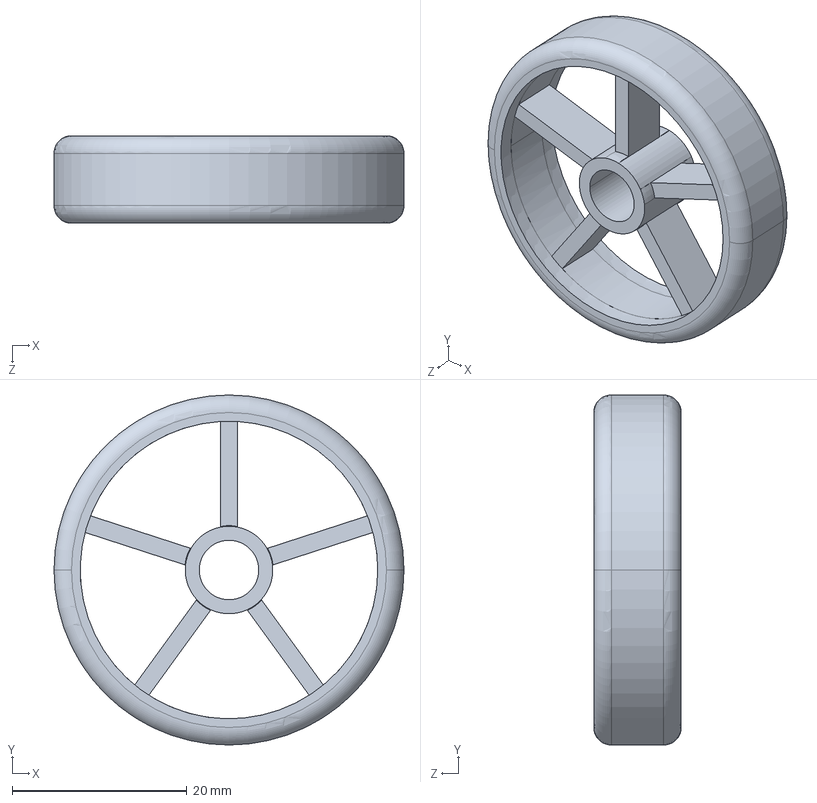
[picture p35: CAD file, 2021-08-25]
Mechanical Designs/Fly Wheel/Simscape/Wheel_Default_sldprt.STEP
40.0 x 40.0 x 10.0 mm

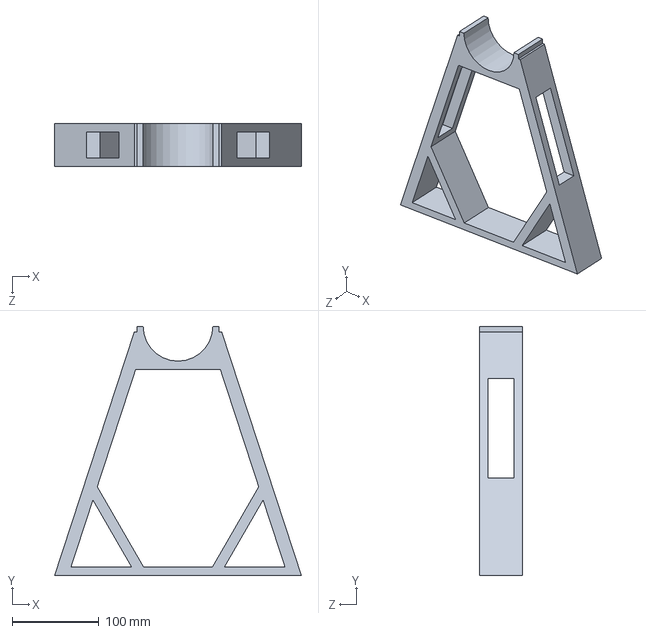
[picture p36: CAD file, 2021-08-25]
Mechanical Designs/Fly Wheel/SolidWorks/Support1.SLDPRT
285.2 x 288.0 x 50.0 mm

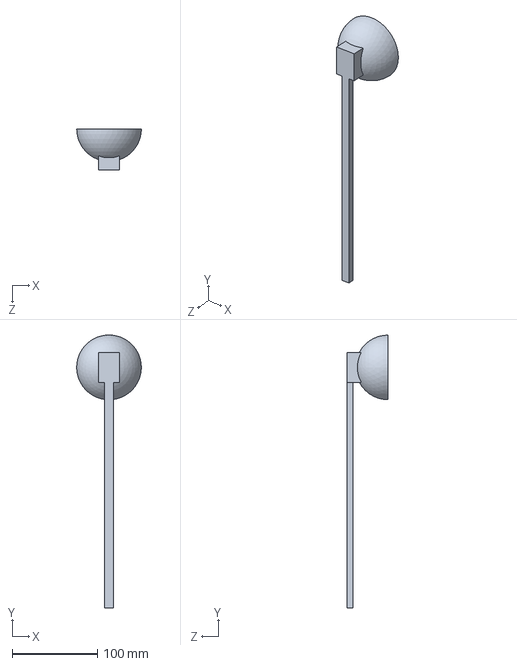
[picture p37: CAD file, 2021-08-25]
Mechanical Designs/Throwing Arm/Simscape/Arm_Default_sldprt.STEP
76.0 x 320.5 x 48.0 mm

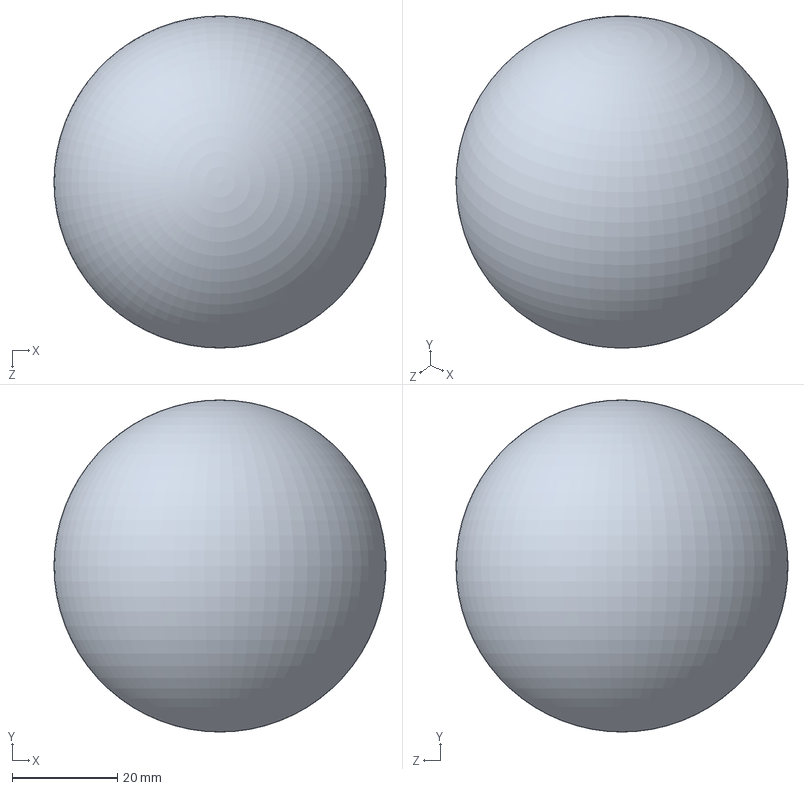
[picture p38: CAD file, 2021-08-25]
Mechanical Designs/Throwing_Arm_Modified/Ball.SLDPRT
63.0 x 63.0 x 63.0 mm

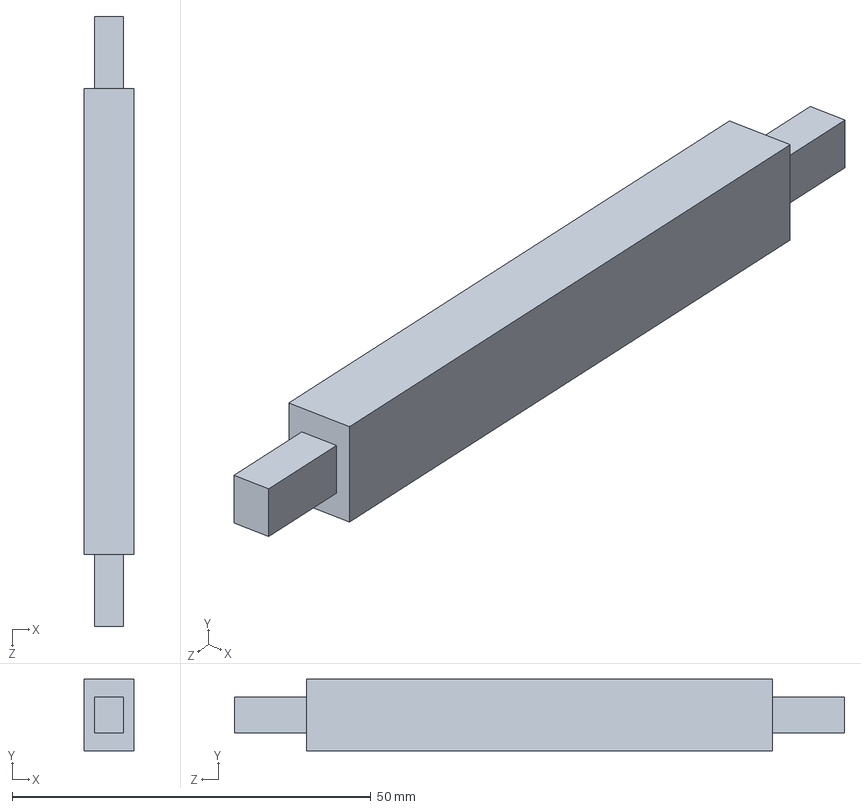
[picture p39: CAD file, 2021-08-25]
Integration/Throwing Arm Modified/Support_W_Default_sldprt.STEP
7.00 x 10.0 x 85.0 mm

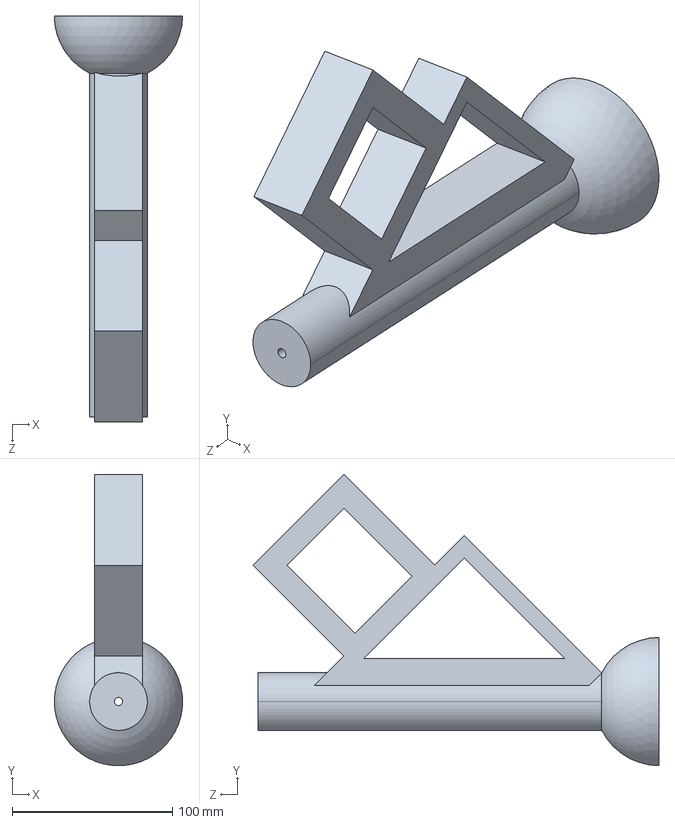
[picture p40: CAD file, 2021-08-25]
Mechanical Designs/Firing Ball/Simscape/Gun_Default_sldprt.STEP
80.0 x 181.7 x 253.2 mm

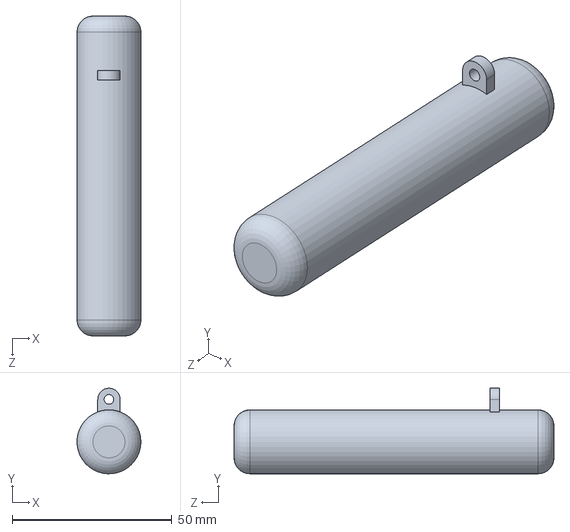
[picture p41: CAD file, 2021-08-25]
Mechanical Designs/Firing Ball/SolidWorks/Shaft_FB.SLDPRT
20.0 x 26.8 x 100.0 mm

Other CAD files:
Mechanical Designs/Throwing Arm/SolidWorks/Arm.SLDPRT
Mechanical Designs/Fly Wheel/Simscape/Shaft_Default_sldprt.STEP
Mechanical Designs/Fly Wheel/SolidWorks/Ball.SLDPRT
Mechanical Designs/Throwing Arm/Simscape/Support_TA_Default_sldprt.STEP
Integration/Throwing Arm Modified/Ball_Default_sldprt.STEP
Integration/Throwing Arm Modified/Base_Default_sldprt.STEP
Integration/Throwing Arm Modified/Beam_Default_sldprt.STEP
Integration/Throwing Arm Modified/Shaft_Default_sldprt.STEP
Integration/Throwing Arm Modified/Support_E_Default_sldprt.STEP
Integration/Throwing Arm Modified/Support_N_Default_sldprt.STEP
Integration/Throwing Arm Modified/Support_S_Default_sldprt.STEP
Mechanical Designs/Firing Ball/Simscape/Ball_Default_sldprt.STEP
Mechanical Designs/Firing Ball/Simscape/Base_FB_Default_sldprt.STEP
Mechanical Designs/Firing Ball/Simscape/Bullet_Default_sldprt.STEP
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

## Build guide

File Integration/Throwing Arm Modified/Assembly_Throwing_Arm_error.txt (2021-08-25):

Constrained Instances: 'Shaft-1', 'Shaft-1', 'Base-1', 'Base-1'
Constraint Name: Width1
Error Details: Constraint is not supported. The constraint has been ignored.
---------------------------------------------------------------------------------

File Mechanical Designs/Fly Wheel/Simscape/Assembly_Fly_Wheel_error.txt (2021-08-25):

Constrained Instances: 'Support1-1', 'Support1-1', 'Slide-1', 'Slide-1'
Constraint Name: Width1
Error Details: Constraint is not supported. The constraint has been ignored.
---------------------------------------------------------------------------------
Constrained Instances: 'spur gear_iso-1', 'spur gear_iso-2'
Constraint Name: GearMate8
Error Details: Constraint is not supported. The constraint has been exported as unknown constraint.
---------------------------------------------------------------------------------
Constrained Instances: 'spur gear_iso-1', 'spur gear_iso-1', 'Housing-1', 'Housing-1'
Constraint Name: Width2
Error Details: Constraint is not supported. The constraint has been ignored.
---------------------------------------------------------------------------------
Constrained Instances: 'Shaft-3', 'Shaft-3', 'spur gear_iso-1', 'spur gear_iso-1'
Constraint Name: Width6
Error Details: Constraint is not supported. The constraint has been ignored.
---------------------------------------------------------------------------------
Constrained Instances: 'spur gear_iso-3', 'spur gear_iso-2'
Constraint Name: GearMate9
Error Details: Constraint is not supported. The constraint has been exported as unknown constraint.
---------------------------------------------------------------------------------
Constrained Instances: 'Shaft-2', 'Shaft-2', 'spur gear_iso-2', 'spur gear_iso-2'
Constraint Name: Width5
Error Details: Constraint is not supported. The constraint has been ignored.
---------------------------------------------------------------------------------
Constrained Instances: 'spur gear_iso-4', 'spur gear_iso-3'
Constraint Name: GearMate10
Error Details: Constraint is not supported. The constraint has been exported as unknown constraint.
---------------------------------------------------------------------------------
Constrained Instances: 'Shaft-1', 'Shaft-1', 'spur gear_iso-4', 'spur gear_iso-4'
Constraint Name: Width4
Error Details: Constraint is not supported. The constraint has been ignored.
---------------------------------------------------------------------------------
Constrained Instances: 'Housing-1', 'Housing-1', 'Slide-1', 'Slide-1'
Constraint Name: Width7
Error Details: Constraint is not supported. The constraint has been ignored.
---------------------------------------------------------------------------------

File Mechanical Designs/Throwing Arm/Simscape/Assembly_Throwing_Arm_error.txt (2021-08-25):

Constrained Instances: 'Shaft-1', 'Shaft-1', 'Frame-1', 'Frame-1'
Constraint Name: Width1
Error Details: Constraint is not supported. The constraint has been ignored.
---------------------------------------------------------------------------------
Constrained Instances: 'Support_TA-2', 'Support_TA-2', 'Frame-1', 'Frame-1'
Constraint Name: Width5
Error Details: Constraint is not supported. The constraint has been ignored.
---------------------------------------------------------------------------------

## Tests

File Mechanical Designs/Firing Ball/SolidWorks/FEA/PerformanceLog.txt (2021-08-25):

Number of Contacts: 1
Number of contact data: 1217
